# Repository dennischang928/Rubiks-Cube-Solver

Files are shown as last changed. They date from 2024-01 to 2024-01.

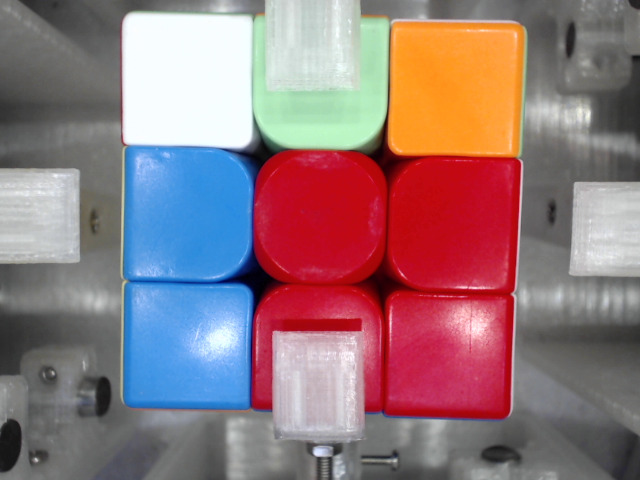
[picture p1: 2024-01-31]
Paper/DX.jpeg

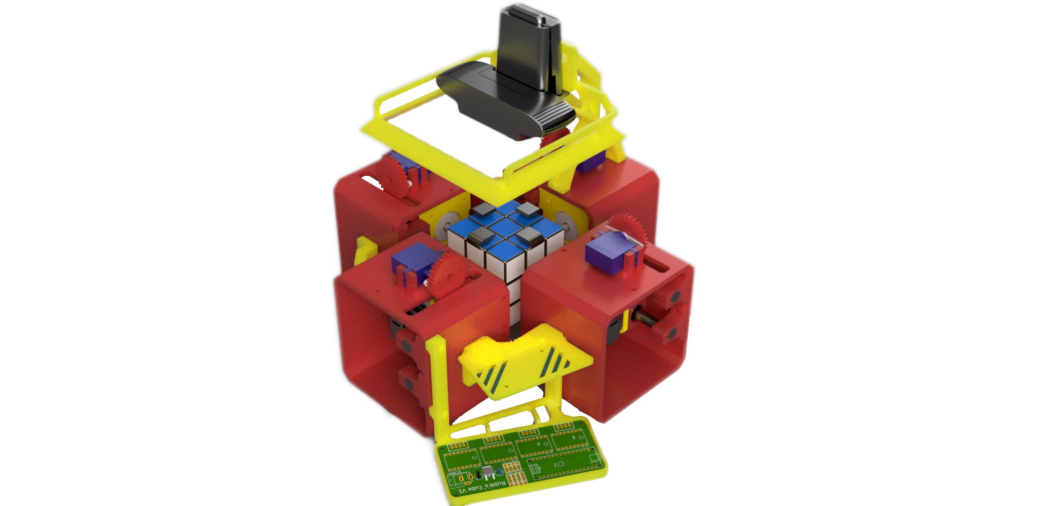
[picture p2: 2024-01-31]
Posters/Rubik_cube_solver_combine v50.png

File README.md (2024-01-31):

SubPage
# Rubik's-Cube-Solving-Robot

# Abstract

Rubik's Cube, a 3-D combination puzzle invented by Ernő Rubik in 1974, is the World’s top-selling puzzle game and best-selling toy. Rubik's Cube is surprisingly complex, there are 43,252,003,274,489,856,000 permutations of a standard 3×3×3 Rubik's Cube. Although humans are impossible to memorize all permutations of a Rubik’s Cube, humans can solve the puzzle as fast as 3.47 seconds. In recent years, a robot developed by MIT students can solve it in 0.38 seconds using an optimal algorithm.
In this project, I developed a Rubik’s Cube-solving robot using a Computer Vision algorithm from scratch. The robot has 4 stepper motors and 4 servo motors as actuators. A camera is included to observe each color arrangement of the face of the Cube in a scrambled state sequentially. The image that the camera observed will be sent through a serial interface to the computer. I implement a solving algorithm that will take the Cube state as input and the sequence of moves that solve the Cube as an output. The sequence of moves is sent to the MCU and is then translated into a series of instructions. The stepper motors and the servo motors then work together to twist the Cube according to the instructions, fully solving the Cube.

# Contents

- Abstract
- Motivation
- Introduction
- Materials
- Designs
  - Hardware
    - Actuators
    - Camera
    - Electronics
  - Programming
    - Computer vision
    - Thistlethwaite's algorithm
    - Firmware
- Challenges and Conclusion
- Reference
- Appendix — Workflow of the Rubik's Cube solving robot

# Motivation

In recent years, Computer Vision becomes more popular. Computer Vision has a lot of applications, such as object detection, event detection, video tracking, and color recognition. To familiarize myself in the field, I decide to develop a robot that solves a Rubik’s Cube using Computer Vision.
The goal is to fully solve a Rubik’s cube by twisting it using clamps attached to stepper and Servo motors. We will use a camera to capture each face of the cube. A computer will then be used, using the computer vision algorithm, to process these images and find out the color of the 9 stickers in each face. Once the color states of the cube are determined, the computer can then compute the sequence of moves that fully solve the cube.

# Introduction

I design the robot using Fusion 360 and Eagle. This robot consists of 4 stepper and Servo motors, 4 pairs of 3d-printed clamp and frame, a camera, and a PCB board with a microcontroller and 4 stepper motor drivers.



The design of the robot ^

To know the initial state of the Cube, I use a camera to capture the color of the Cube. Since the camera can only capture a single face of the Cube each time, the robot needs to rotate the Cube for the camera to capture all the faces of the cube. After capturing, the camera is going to send those images to the computer through a USB port.

The computer will then detect the position and orientation of each face from all 6 images. By using these information, the computer can find out the position and area of each sticker of the Cube in those images. The computer can now extract the color of each sticker, and determine the color of each sticker using computer vision.

Once the initial state of the Cube is found, the computer solves the Cube using Thistlethwaite's algorithm. The solution, the sequence of moves represented in Rubik's Cube Notation, will then be sent from the computer to the microcontroller. Afterwards, the microcontroller translates these notations into a series of stepper and Servo motors movements that twist the Cube and fully solve the Cube.

# Materials

- 4 stepper and Servo motors
- 4 3d-printed clamps attached to the stepper motors
- An Arduino nano and 4 stepper motor drivers
- A DC transformer
- A fill light

# Designs

## Hardware

### Actuators

To physically twist and rotate the cube, I use 4 NEMA 17 stepper motors that use a clamp to clip and twist 4 individual faces of the cube. I have considered using DC motors and brushless motors, but both of them can't know their physical rotated-angle without an encoder, so they can't twist the cube precisely.

I have considered using DC motors and brushless motors, but both of them can't twist the Cube precisely because their physical rotated-angle cannot be determined without an encoder.

Although Servo motors can rotate precisely to an angle, most Servo motors can only rotate from 0 degrees to 180 degrees. <add a reason why 0-180 is bad> Therefore, I decided to use stepper motors because they are continuous(they can rotate in one direction infinitely) and can rotate precisely. Therefore, a stepper motor will perfectly fit our use case.

Stepper motors operate using a coil to attract the permanent magnets that encircle the center axle. By energizing the coils, the axle of the motor can rotate precisely by 1.8 degrees. (Stepper motors take 200 steps to make a complete rotation, so its resolution is 1.8 degree = (360° /200 steps))

Stepper motors move in steps. For example, a stepper motor with 200 steps resolution will rotate 1.8 degrees angle for one step (360° / 200 steps).



Simplified stepper motor rotates 3 steps.

Stepper motor is an Open Loop Control System, we don't know its position upon start-up.

In order to twist the Cube properly, the clamp needs to be aligned vertically with the Cube. Therefore, I design a device that uses a distance sensor to provide feedback for the motor to align the clamp and the cube. The device consists of a disk attached to the axle of the motor and an IR Sensor facing the disk. The cube and clamp are in perfect alignment when the IR Sensor faces the hole directly. Hence, by reading the sensor value, the motor can rotate the clamp until it aligns perfectly with the cube.

螢幕截圖 2021-08-16 17.51.25.png

螢幕截圖 2021-08-16 17.51.08.png

IMG_2260.HEIC



Fig 1

I found a problem when the clamp is twisting the cube. If one of the clamps rotates horizontally, the clamps on its left and right can't twist the cube because the clamp that is horizontal blocks their rotation. Tj is also a Servo motor that is responsible to separate the clamp from the cube so that all clamps can rotate freely. As shown in the image on the left

In contrast to the stepper motor, Servo motor is a Closed Loop control system. When the Servo motor is moving, the position given by the potentiometer as feedback (Fig 1)
is sent to the Servo motor control board to ensure it rotates to the expected position.

I use Rack and pinion mechanics to convert the rotational motion of the Servo motor into linear motion to separate the clamp from the cube.

螢幕截圖 2021-08-17 11.19.00.png

### Camera

To determine the initial state of a Rubik's cube, I use a camera to capture the color of each face of the Rubik's cube. I chose a Logitech Webcam as the camera because it has HD resolution and an autofocus function. Moreover, the camera allows you to adjust the brightness, sharpness, contrast, and saturation of the image. By adjusting these values, the images will become sharper and easier for the computer to distinguish colors.

Trying to distinguish color from the image that the camera sends to the computer, I find that if the ambient light around the cube is unstable, the color recognition program will be extremely inaccurate. To make sure the projected light on the cube is consistent, I added an artificial light source to maintain the brightness of the image. Therefore, I use 4 LED strings to supply light in 4 directions, so the brightness anywhere on the face of the cube is the same.

### Electronics

Instead of using a commercial CNC control board that can control stepper motors easily, I am going to design my robot controller PCB that can control 4 stepper motors and 4 Servo motors of my robot because most commercial CNC control boards can't control 2 or more Servo motors. Also, there is a lot of limitations of programming these commercial PCB board, so I decided to make my own control board.



Robot control board

- Microcontroller

In order to control the whole robot, I decided to use Arduino nano to control the whole system because it is smaller than Arduino UNO and easy to program. Arduino Nano has a built-in Mini USB jack, so it can communicate with the computer through a Serial port with the Mini USB jack.

- Stepper Motor Control

Although stepper motors have a lot of advantages, controlling stepper motors often require sufficient and controlled energy for phases in a precise sequence, so a driver is often needed. Due to this, I plan to use 4 A4988 stepper motor drivers to control all of my stepper motors of the robot.

Each A4988 motor driver required 2 control signal pins (step, direction) and 3 setup signal pins(MS1, MS2, MS3). The step and direction pins are used to control the movement of the stepper motors. The direction pin controls the rotating direction of the motor, and we can control the movement of a step of the motor by sending a pulse to the step pin. The MS1, MS2, MS3 pins are used to control the step of the stepper motor. By changing the input state of these pins to logic low or logic high, you can select one of the five steps resolutions according to the table(Fig 2).



Fig 2

- Servo motors Control

A Servo motor can be controlled by sending a series of pulses through the signal pin. By changing the width of these pulses, we can control the Servo motor rotates to different angles.



How pulses with different widths control the Servo motor

## Programming

### Computer visions

In order to determine the color arrangement of each of the images captured by the camera precisely, I implemented a method that can find out the difference between two colors.
A color model is a visualization that depicts the color spectrum as a multidimensional model. There are some commonly used color models in the world. Most modern color models have 3 dimensions (like RGB and HSV), while other models have more dimensions (like CMYK), and I am going to compare these different color models and find out which of them are more reliable in this project.

---

- RGB

  RGB is a 3-dimensional color model. RGB color model represents a color by mixing three different colors (Red, Green, and Blue). Although RGB color model is commonly used in our daily life, RGB color model is a non-uniform color model, which means the Euclidian distance of two colors represented by the RGB color model does not correspond to the color difference perceived by humans.

  _Euclidian distance:_

  $distance=√((R2−R1)^2+(G2−G1)^2+(B2−B1)^2)$

  

---

- HSV

  HSV is a cylindrical color model that remaps the RGB primary colors into dimensions that are easier for humans to understand.

  In HSV color model, we can represent a color with 3 variables (Hue, Saturation, Value). Hue controls the angle of the color on the RGB color circle; Saturation controls the amount of color used; Value controls the brightness of the color.

  

  HSV (cylindrical color model)

---

- CIELAB

  CIELAB color model is three-dimensional, you can represent a color with 3 variables in CIELAB color model while L stands for perceptual lightness, and A and B stand for the four unique colors of human vision: red, green, blue, and yellow. In short, CIELAB is designed to approximate human vision, so it can describe a color more accurate than RGB and HSV color models can.

  

  CIELAB color space top view

According to the comparison, I think using CIELAB color model in the Computer Vision method has a lot of advantages, so I plan to use CIELAB color model to represent a color in the Computer Vision method.

When the computer wants to distinguish which color (orange, white, blue, red, yellow, green) of a sticker is, the most important thing is to find out the distance between the sticker pixel color and the reference colors, so the computer can then compare the distance between these reference colors, and distinguish the color. In order to get the color difference between two colors reliably, I use a CIEDE2000 ΔE method instead of the Euclidean distance method because the CIEDE2000 ΔE method is more reliable for human vision.

Given a reference color (L*1, a*1, b*1) and another color (L*2, a*2, b*2), the CIEDE2000 difference of these 2 colors is:



CIEDE2000 ΔE formula
[https://en.wikipedia.org/wiki/Color_difference](https://en.wikipedia.org/wiki/Color_difference)

Where:

[https://wikimedia.org/api/rest_v1/media/math/render/svg/2940920f995d52312ede05214ffa3c60f0db9b7f](https://wikimedia.org/api/rest_v1/media/math/render/svg/2940920f995d52312ede05214ffa3c60f0db9b7f)

CIEDE2000 ΔE formula
[https://en.wikipedia.org/wiki/Color_difference](https://en.wikipedia.org/wiki/Color_difference)

Because of the rotation of the cube, the cube position may always shift when scanning the cube, so I have to frequently adjust the cube detect area of the camera manually before scanning it, and I think that adjusting the cube manually is annoying, especially when I'm debugging the program.

Then, I try to implement a cube position tracking program in the solver, so that the solver can adjust the detect area automatically.

The tracking program is actually dum. First of all, the program is going to make the dimmer place of the image more dimmer; the brighter place brighter. The program can then find out the position of the centerpiece of the cube by comparing the pixel of the filtered image. The program can then find out the position of other pieces.



Image before filter



Filtered image

### Thistlethwaite's algorithm

After finding the state of the cube, the computer will then solve the cube using Thistlethwaite's algorithm. Thistlethwaite's algorithm is a famous algorithm devised by Morwen B. Thistlethwaite.

Before I explain how the algorithm works, we first have to know how do people represent a twist of a cube. People usually use a notation called Rubik's Cube Notation to represent a twist of a cube. The twist of a Rubik's Cube is classified into three categories of Notations (clockwise twist, counterclockwise twist, double clockwise twist).

- The notation with only one letter refers to a clockwise face twist in 90 degrees (quarter turn). "F" refers to a clockwise turn of the Front face in 90 degrees.
- The notation with one letter followed by an apostrophe (') refers to a counterclockwise face twist in 90 degrees (quarter turn). "D'" refers to a counterclockwise turn of the Down face in 90 degrees.
- The notation with one letter followed by the number 2 refers to a clockwise face twist in 180 degrees (double turn). "U2" refers to a clockwise turn of the Up face in 180 degrees.



Thistlethwaite algorithm solves a cube by twisting the cube by a certain set of moves. When the cube reaches a specific state, the cube will "move" from one "group" to another. As the cube reaches another "group", the set of moves of the cube will change and the cube will be easier to solve computationally.

The groups are:

- Group 0:

[https://wikimedia.org/api/rest_v1/media/math/render/svg/2dbdffdebca6e844bdf3c7548a8033992ef6ac79](https://wikimedia.org/api/rest_v1/media/math/render/svg/2dbdffdebca6e844bdf3c7548a8033992ef6ac79)

Required Cube state: This group contains all possible states of the Rubik's Cube.

---

- Group 1:

[https://wikimedia.org/api/rest_v1/media/math/render/svg/116b5e3559d97ddaa688362537461712c1435f10](https://wikimedia.org/api/rest_v1/media/math/render/svg/116b5e3559d97ddaa688362537461712c1435f10)

Required Cube state: All 12 edge pieces are correctly oriented.

After reaching Group 1, The cube can then be solved without using U and D turns.

---

- Group 2:

[https://wikimedia.org/api/rest_v1/media/math/render/svg/ab29e5a1ef0d23014458f9603f6c108b7aec73a6](https://wikimedia.org/api/rest_v1/media/math/render/svg/ab29e5a1ef0d23014458f9603f6c108b7aec73a6)

Required Cube state: All corner pieces are correctly oriented. Also, four of the edge pieces are moved to the correct slice: the front-up, front-down, back-up, and back-down edge pieces are placed in the M slice.

After reaching Group 2, The cube can then be solved without using F, B, U, and D moves.

---

- Group 3:

[https://wikimedia.org/api/rest_v1/media/math/render/svg/b9990ca7e1121afb33509d738d77f1d0c455be62](https://wikimedia.org/api/rest_v1/media/math/render/svg/b9990ca7e1121afb33509d738d77f1d0c455be62)

Required Cube state: All corner pieces are moved to the correct orbit. (A corner is in the correct orbit if it can be moved to its home position with only 180-degree twists.) Also, each edge piece is moved to its home slice.

At that point, the cube can be solved with only 180 degrees turn.

---

- Group 4:

[https://wikimedia.org/api/rest_v1/media/math/render/svg/27929bbe730561ca9eb1540e72756b5674436bb5](https://wikimedia.org/api/rest_v1/media/math/render/svg/27929bbe730561ca9eb1540e72756b5674436bb5)

The final group requires only one state, which is a solved cube.

### Firmware

In this project, I use Arduino nano board as my microcontroller to control the stepper motors and servo motors. I implement an Arduino stepper motor driver library in the Arduino board to control the movement of the Stepper motors. For the Servo motors, I use an Arduino built-in Servo library to control them.



There is a lot of ways to communicate between the computer and the Arduino board, such as I2C, Serial communication, and SPI. I decided to use the Serial communication way because it is widely used in the Arduino board (Every Arduino board has its own Serial port). For an Arduino Nano board, it has a built-in mini-USB jack

Here is a case of communication:

The Computer aims to twist the Cube in U U2 D2:

**Step 1:** The computer sends a command("U U2 D2") to the Solver through the Serial interface.

**Step 2:** The Solver receives the command and controls the Stepper motors and the Servo motors to twist the Cube according to the command.

**Step 3:** After twisting the cube, the Solver will send a signal to the computer. Let the computer knows that it has done the task.



# Challenges and Conclusion

After assembling the Solver, there are some problems that I have experienced. When designing this robot, I aim to use a magnetic encoder to monitor the position of the Stepper motor. After I fully assembled the Solver, I try to read the value of the magnetic encoders by connecting them in parallel using I2C, but then I found that these magnetic encoders have the same I2C addresses, and I can't change the addresses. Therefore, the microcontroller can't read the values of them using I2C, so I have redesigned the robot, and I use a light sensor as the position monitoring sensor instead of a magnetic sensor.

There are also some challenges that I have gone through when I programming the robot, such as the inaccuracy of the color detection. To fix the issue, I add an artificial light source to stabilize the light condition of the cube.

The robot also experienced some issues when the stepper motor rotate. Because the stepper motor provides no feedback to the microcontroller, the stepper motor can't affirm a perfect 90 degrees twist is executed. Also, there are gaps between the clamp and the Cube, so there will be some degrees of error when twisting the cube. As a result, slight errors accumulated in the alignment of the Cube after a twist. Because of the alignment of the Cube, the rotation of the stepper motor may be stuck, but the stepper motor can't realize that it is stuck, and it will keep executing the following twists.

Were I to continue work on this project, the following attributes would be changed:

- A Feedback would be added to affirm a perfect 90 degrees twist is executed
- Reduce the size of the Robot.
- Design an adjustable clamp, so that the solver can fit any size of 3\*3 Rubik's Cube.

# Appendix — Workflow of the Rubik's Cube solving robot:

WorkFlow diagram of a Solver.svg

Rubik's Cube Solving Robot test:
[https://youtu.be/ZOZHCysa5HY](https://youtu.be/ZOZHCysa5HY)

# Reference

- Color models and color spaces [https://programmingdesignsystems.com/color/color-models-and-color-spaces/](https://programmingdesignsystems.com/color/color-models-and-color-spaces/)
- Color difference - Wikipedia [https://en.wikipedia.org/wiki/Color_difference](https://en.wikipedia.org/wiki/Color_difference)
- How to control stepper motor with A4988 driver and Arduino [https://howtomechatronics.com/tutorials/arduino/how-to-control-stepper-motor-with-a4988-driver-and-arduino/](https://howtomechatronics.com/tutorials/arduino/how-to-control-stepper-motor-with-a4988-driver-and-arduino/)
- jeswiezy_Project_Final_Report
  [http://web.mit.edu/6.111/www/f2017/projects/jeswiezy_Project_Final_Report.pdf](http://web.mit.edu/6.111/www/f2017/projects/jeswiezy_Project_Final_Report.pdf)
- Thistlethwaite's 52-move algorithm
  [https://www.jaapsch.net/puzzles/thistle.htm](https://www.jaapsch.net/puzzles/thistle.htm)
- Rubik’s Cube Reconstruction from Single View for Service Robots
  [https://www.ia.pw.edu.pl/~wkasprza/PAP/ICCVG06.pdf](https://www.ia.pw.edu.pl/~wkasprza/PAP/ICCVG06.pdf)
- All About Stepper Motors
  [https://learn.adafruit.com/all-about-stepper-motors/what-is-a-stepper-motor](https://learn.adafruit.com/all-about-stepper-motors/what-is-a-stepper-motor)

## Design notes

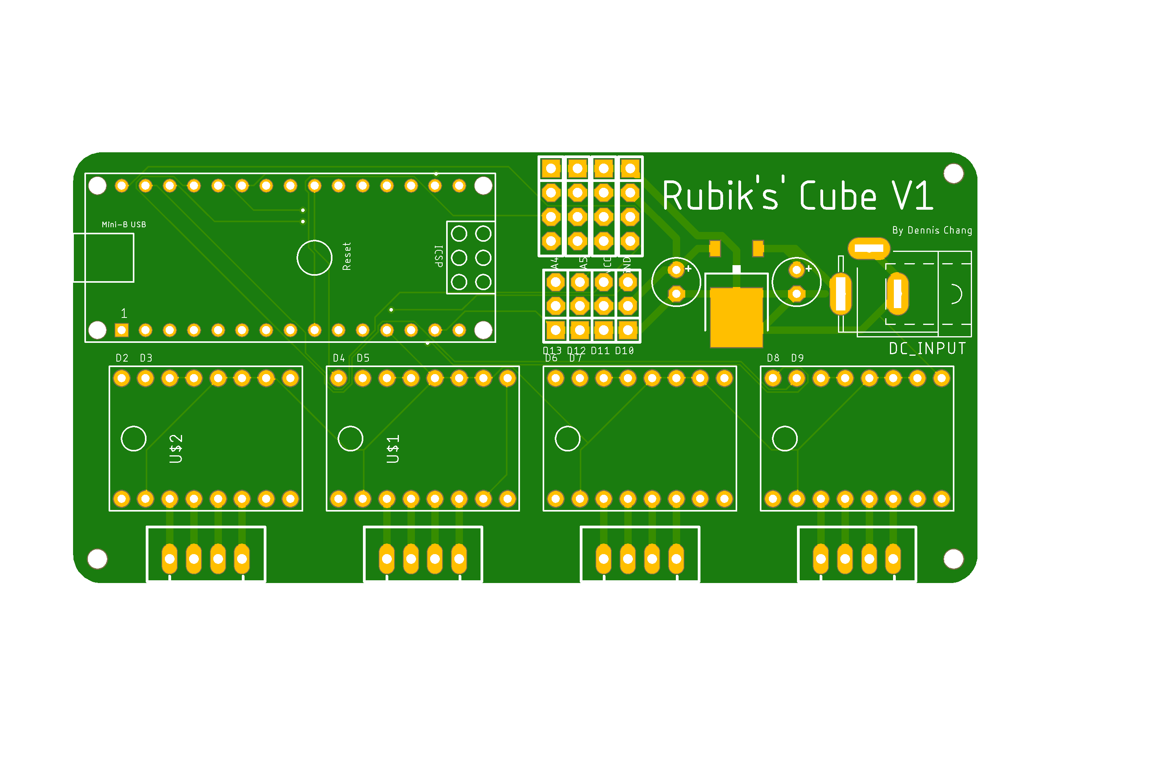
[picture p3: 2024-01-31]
Design/Circuit/V1.png

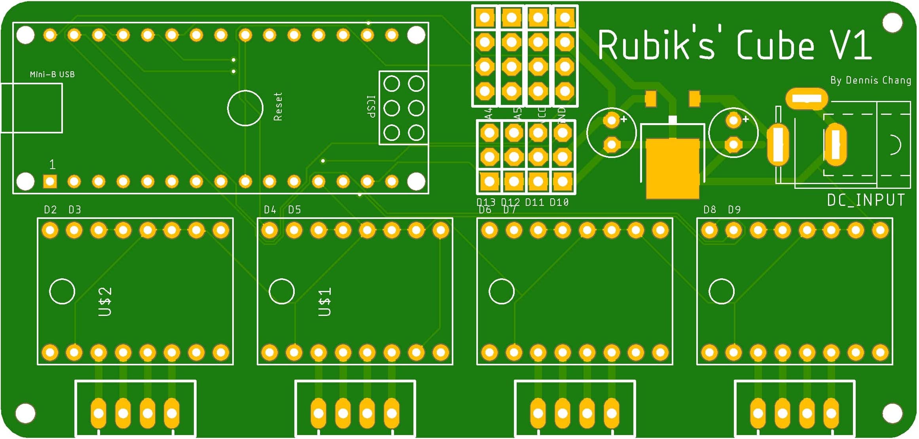
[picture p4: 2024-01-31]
Posters/PCB.jpeg

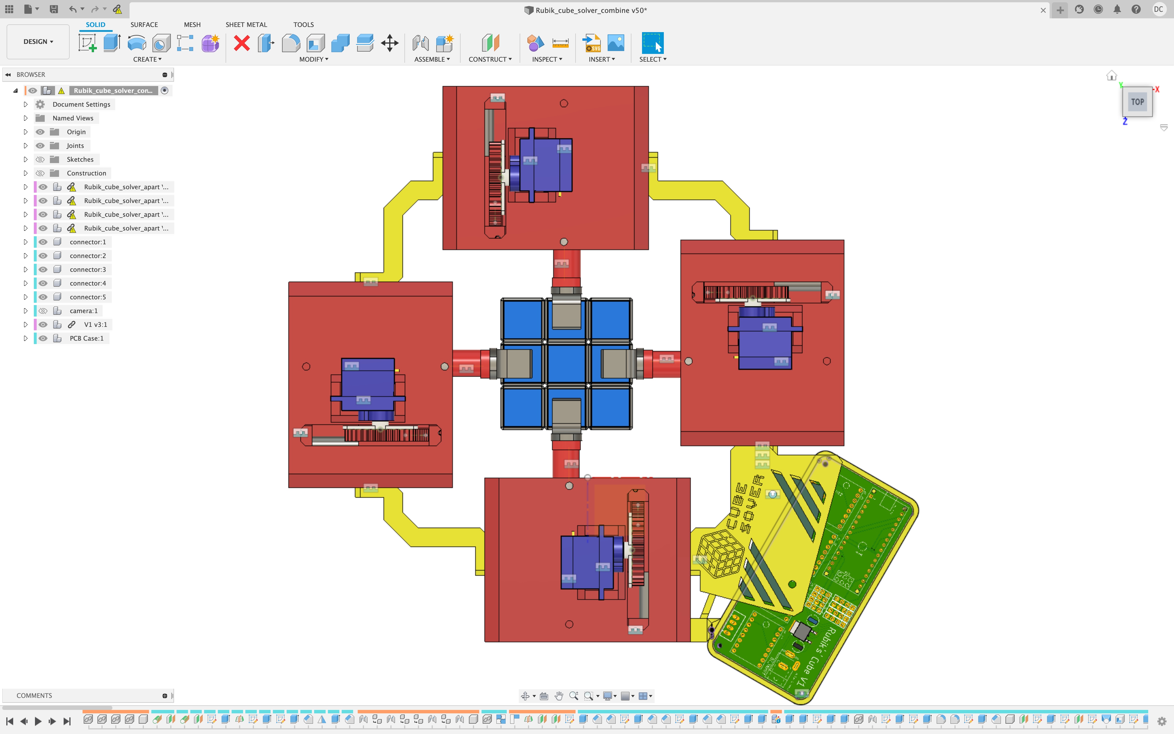
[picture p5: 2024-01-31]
Posters/螢幕截圖 2021-09-24 22.40.52.png

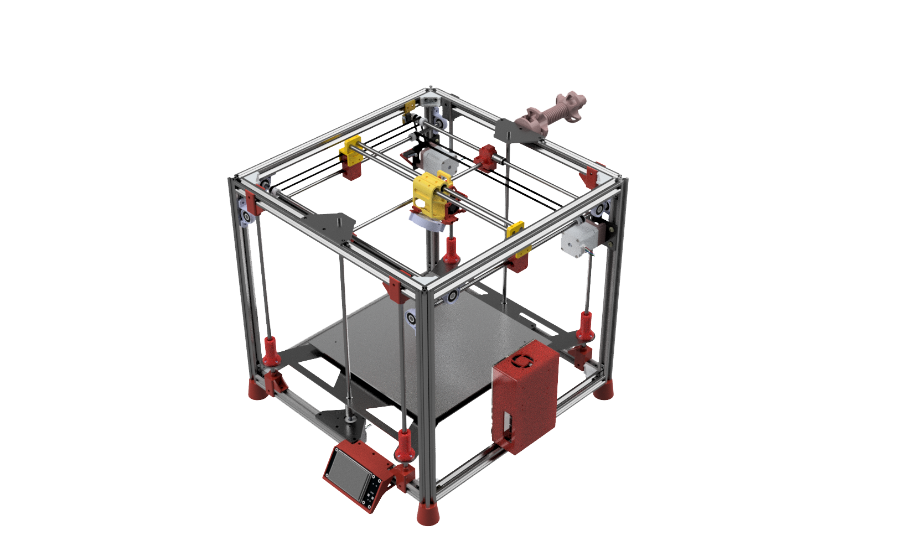
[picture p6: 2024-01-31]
Posters/3dp 5 MK2 v33.png

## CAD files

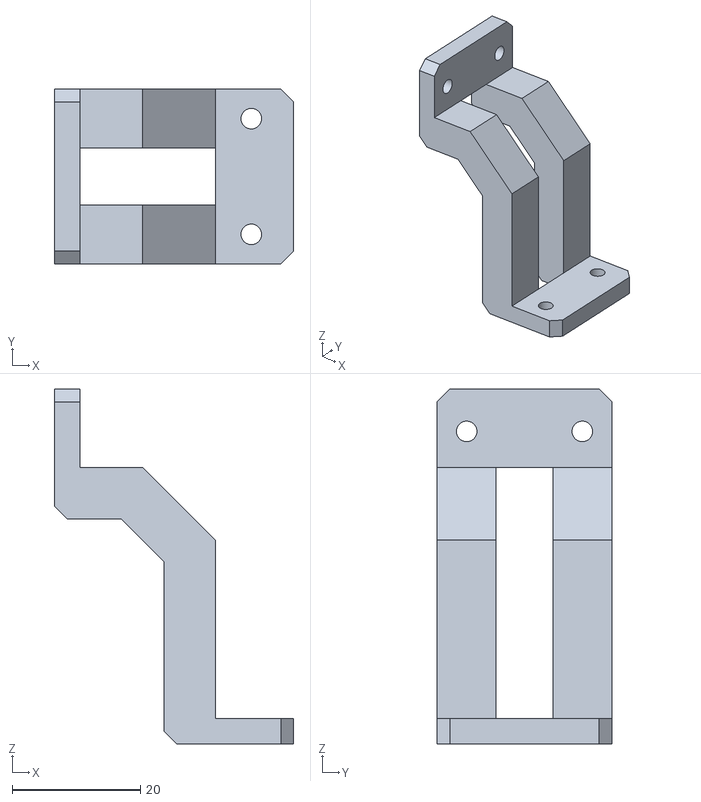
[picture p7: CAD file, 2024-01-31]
stl/com_connect.stl
37.3 x 27.2 x 55.3

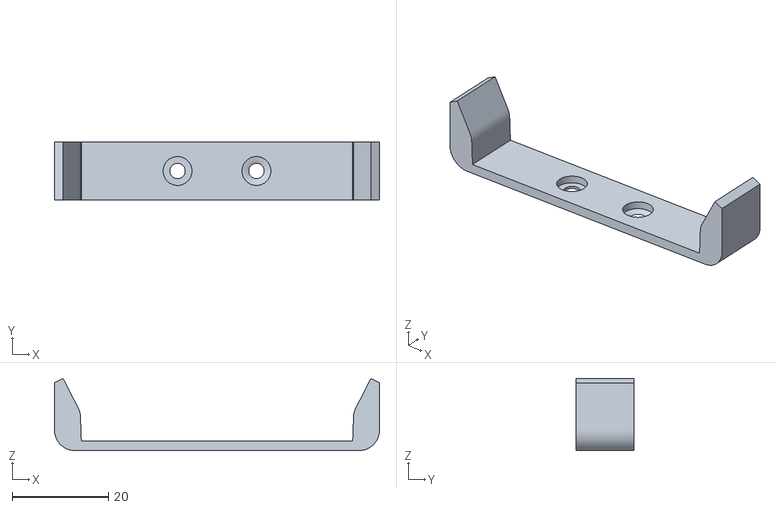
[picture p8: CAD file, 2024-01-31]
stl/v2stl/clips1.stl
67.6 x 12.1 x 15.0

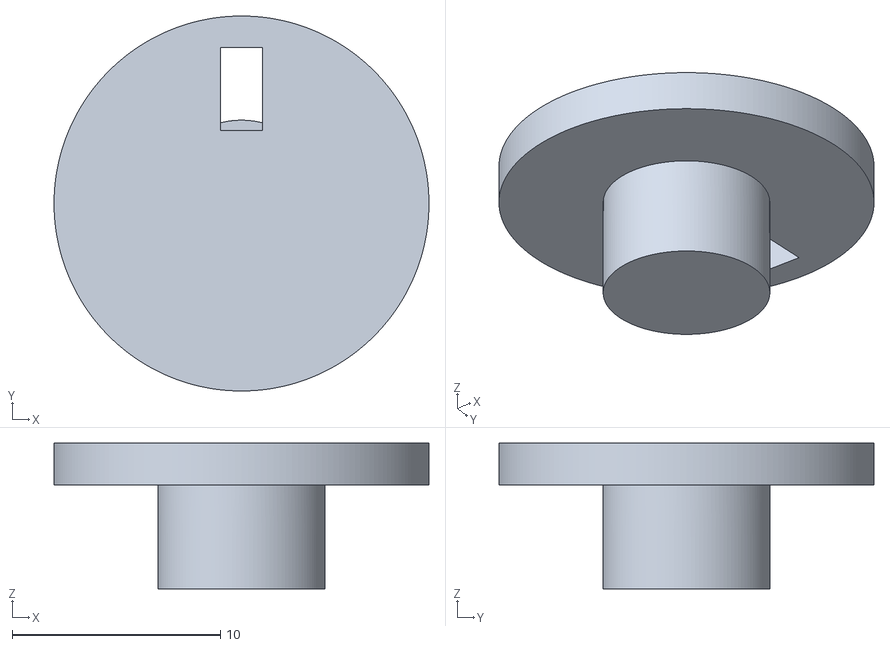
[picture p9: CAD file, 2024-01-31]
stl/rotation plate.stl
18.0 x 18.0 x 7.00

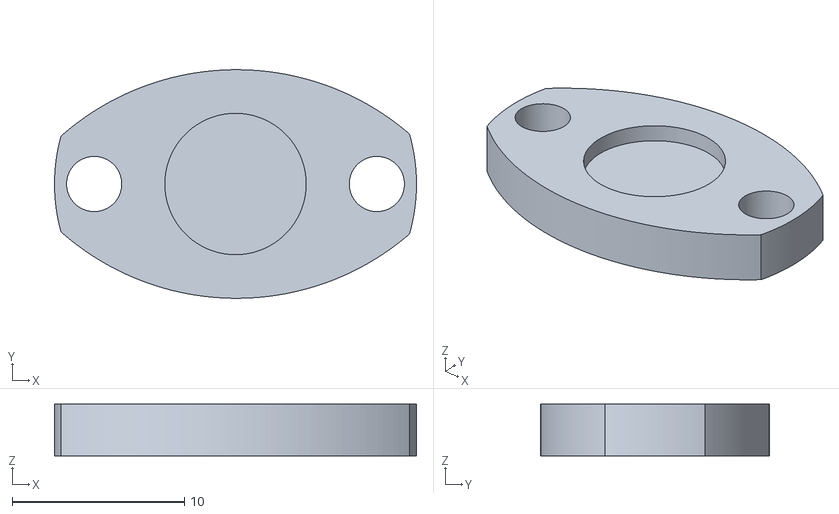
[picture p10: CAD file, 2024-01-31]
stl/v2stl/clips2.stl
21.0 x 13.3 x 3.00

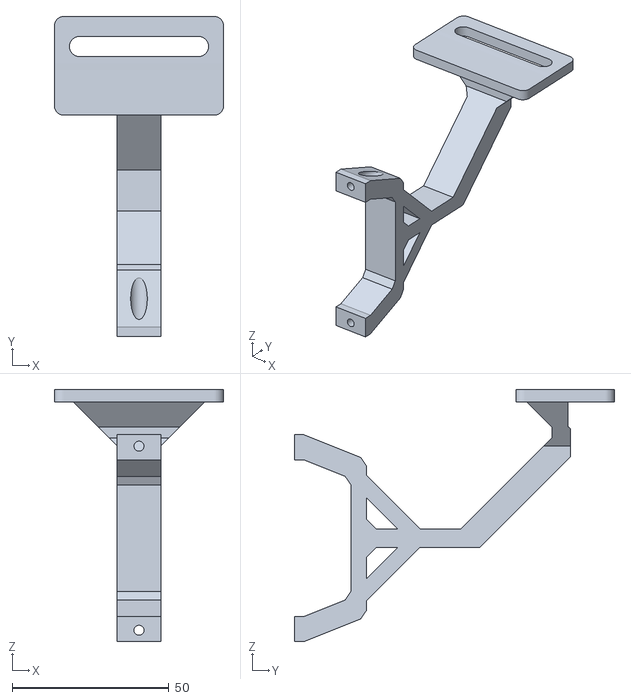
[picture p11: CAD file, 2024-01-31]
stl/camera connector.stl
54.0 x 102.1 x 80.5

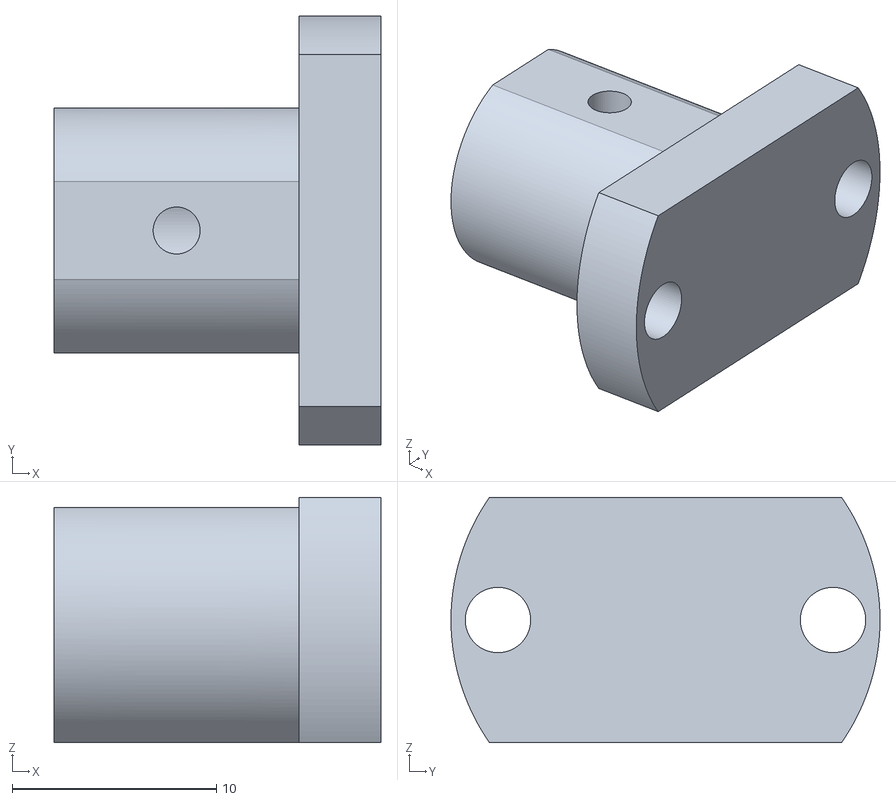
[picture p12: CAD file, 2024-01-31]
stl/v2stl/connector.stl
16.0 x 21.0 x 12.0

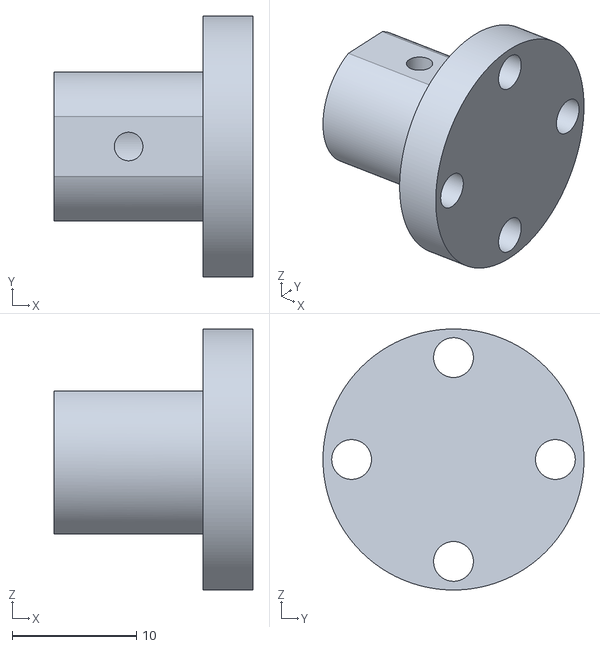
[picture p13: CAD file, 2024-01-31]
stl/stepper_connector.stl
16.0 x 21.0 x 21.0

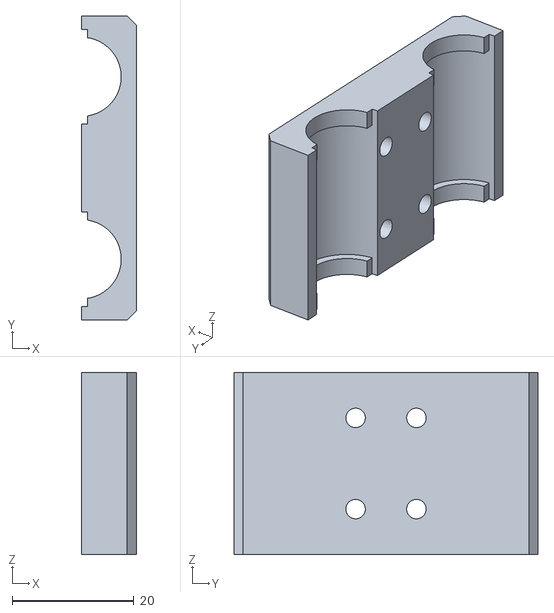
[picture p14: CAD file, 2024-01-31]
stl/move2.stl
9.00 x 50.0 x 30.0

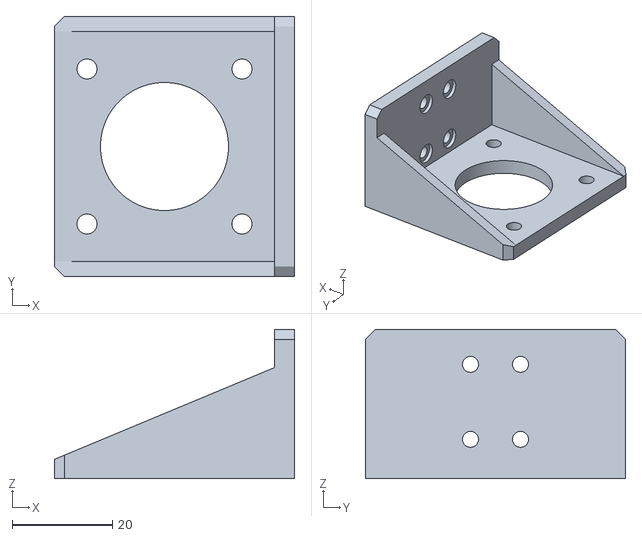
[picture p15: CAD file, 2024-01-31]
stl/stepper.stl
48.0 x 52.0 x 29.9

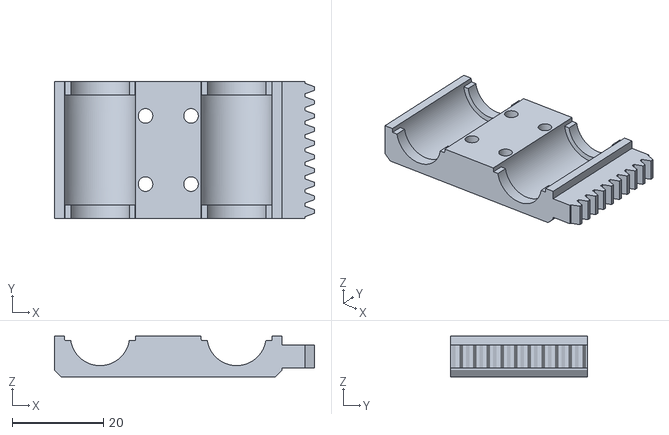
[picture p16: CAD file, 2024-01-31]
stl/move1.stl
57.1 x 30.0 x 9.00

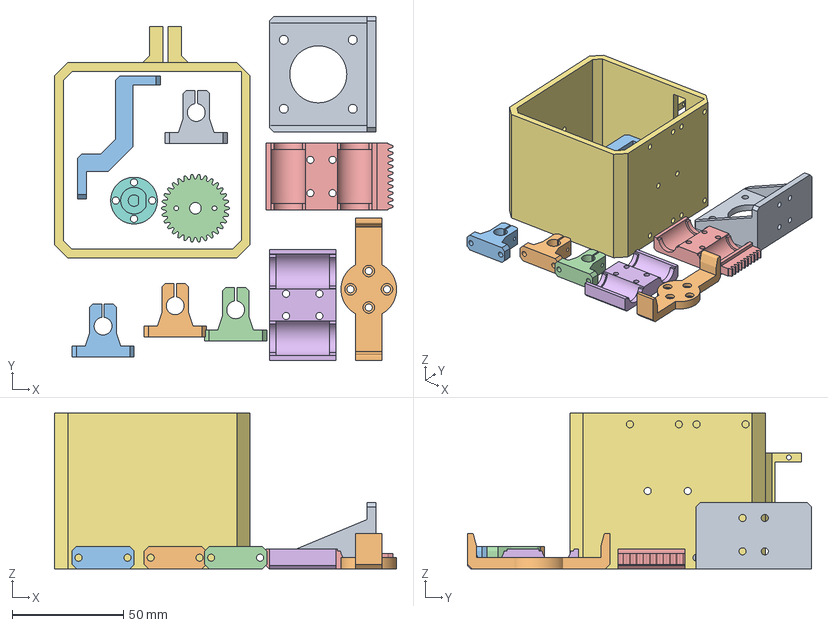
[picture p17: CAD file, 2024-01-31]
stl/rubik's cube v2.3mf
153.8 x 154.7 x 70.0 mm
axis con.stl x 4
clip.stl
com_connect.stl
gear.stl
move1.stl
move2.stl
shell.stl
stepper_connector.stl
stepper.stl

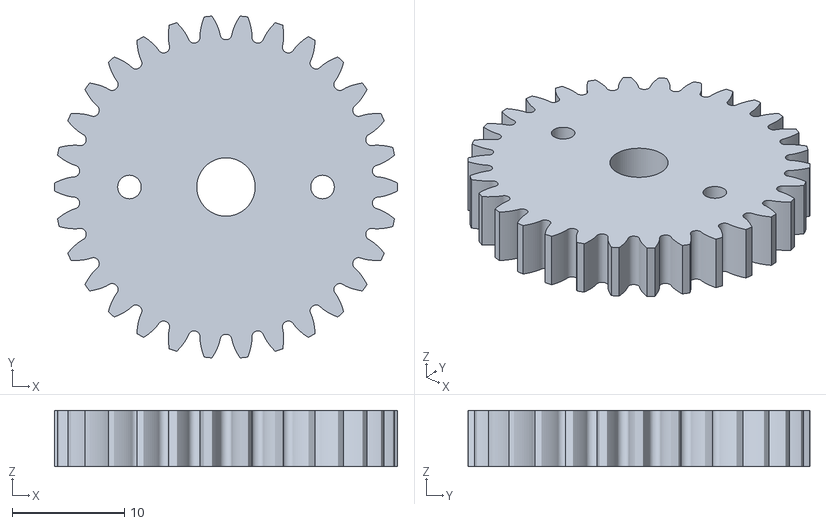
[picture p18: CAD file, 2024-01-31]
stl/gear.stl
30.6 x 30.5 x 5.00

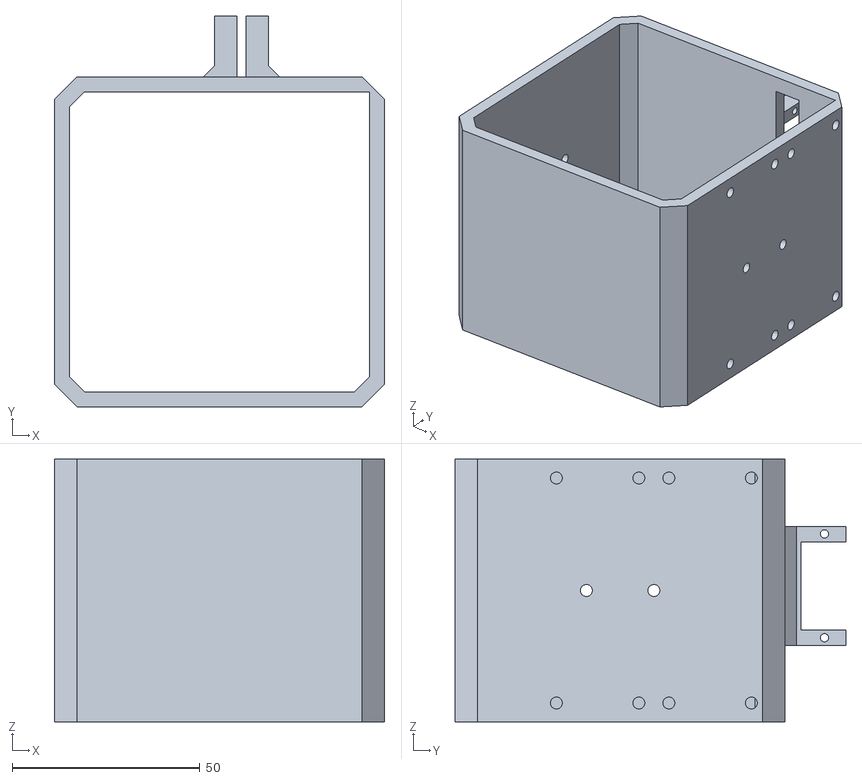
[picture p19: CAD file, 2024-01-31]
stl/shell.stl
88.0 x 104.2 x 70.0

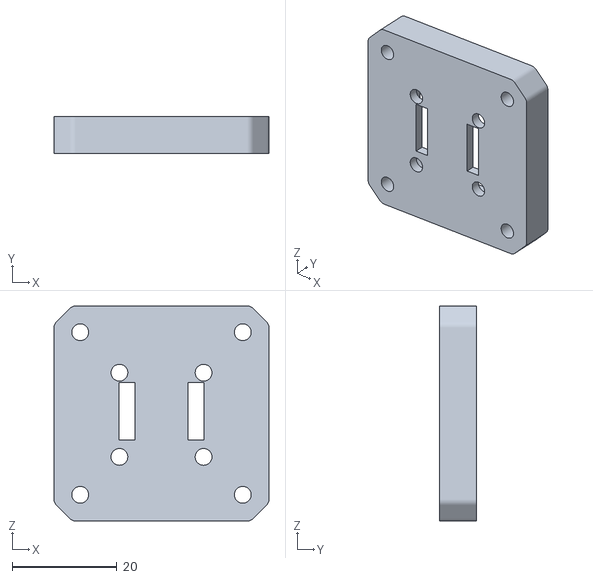
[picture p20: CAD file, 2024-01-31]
stl/encoder_Cover.stl
41.0 x 7.00 x 41.0

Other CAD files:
Pic/Untitled.dwg
stl/encoder.stl
stl/axis con.stl
stl/clip.stl

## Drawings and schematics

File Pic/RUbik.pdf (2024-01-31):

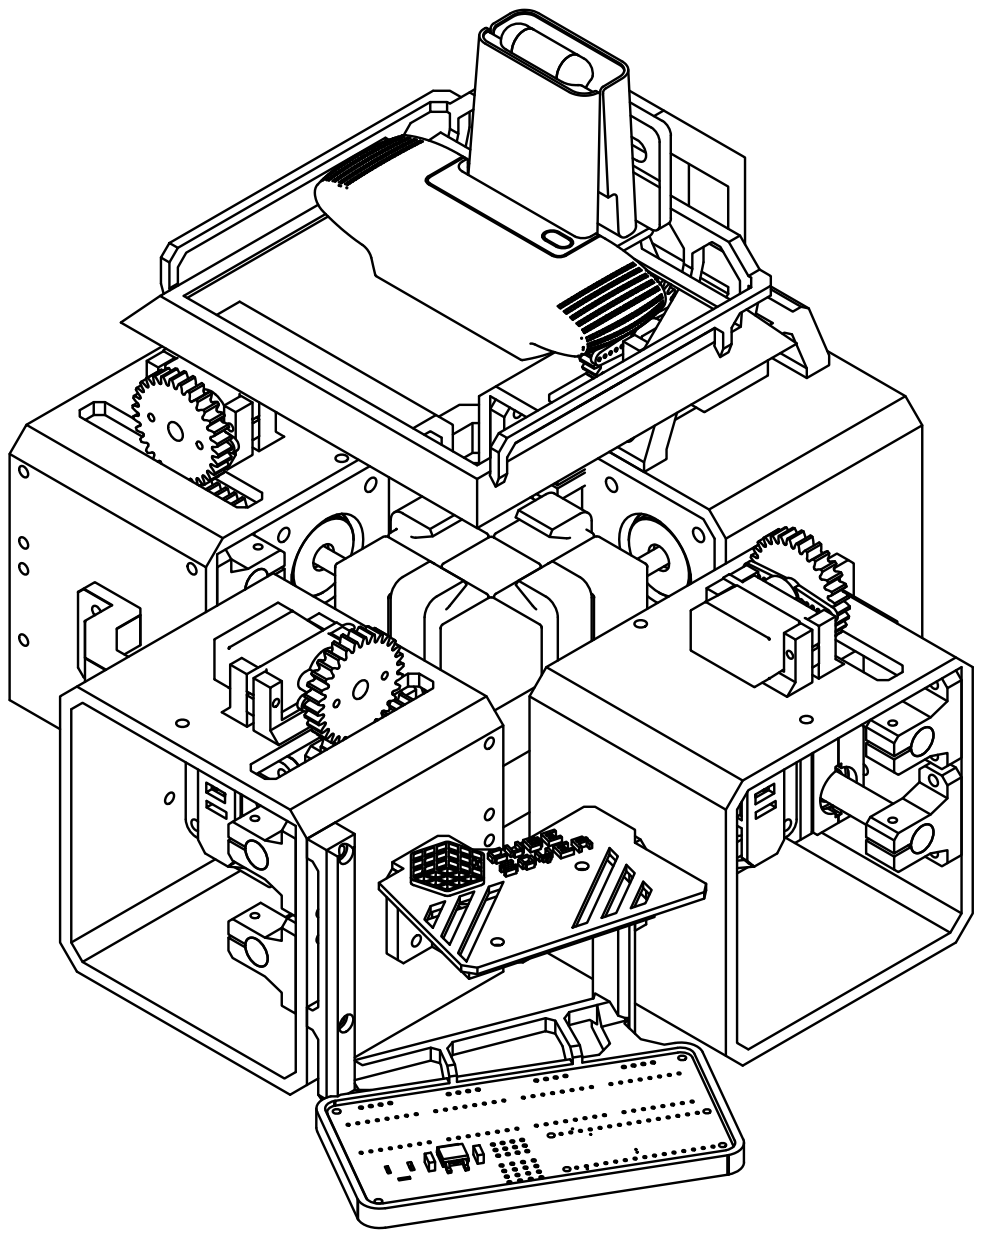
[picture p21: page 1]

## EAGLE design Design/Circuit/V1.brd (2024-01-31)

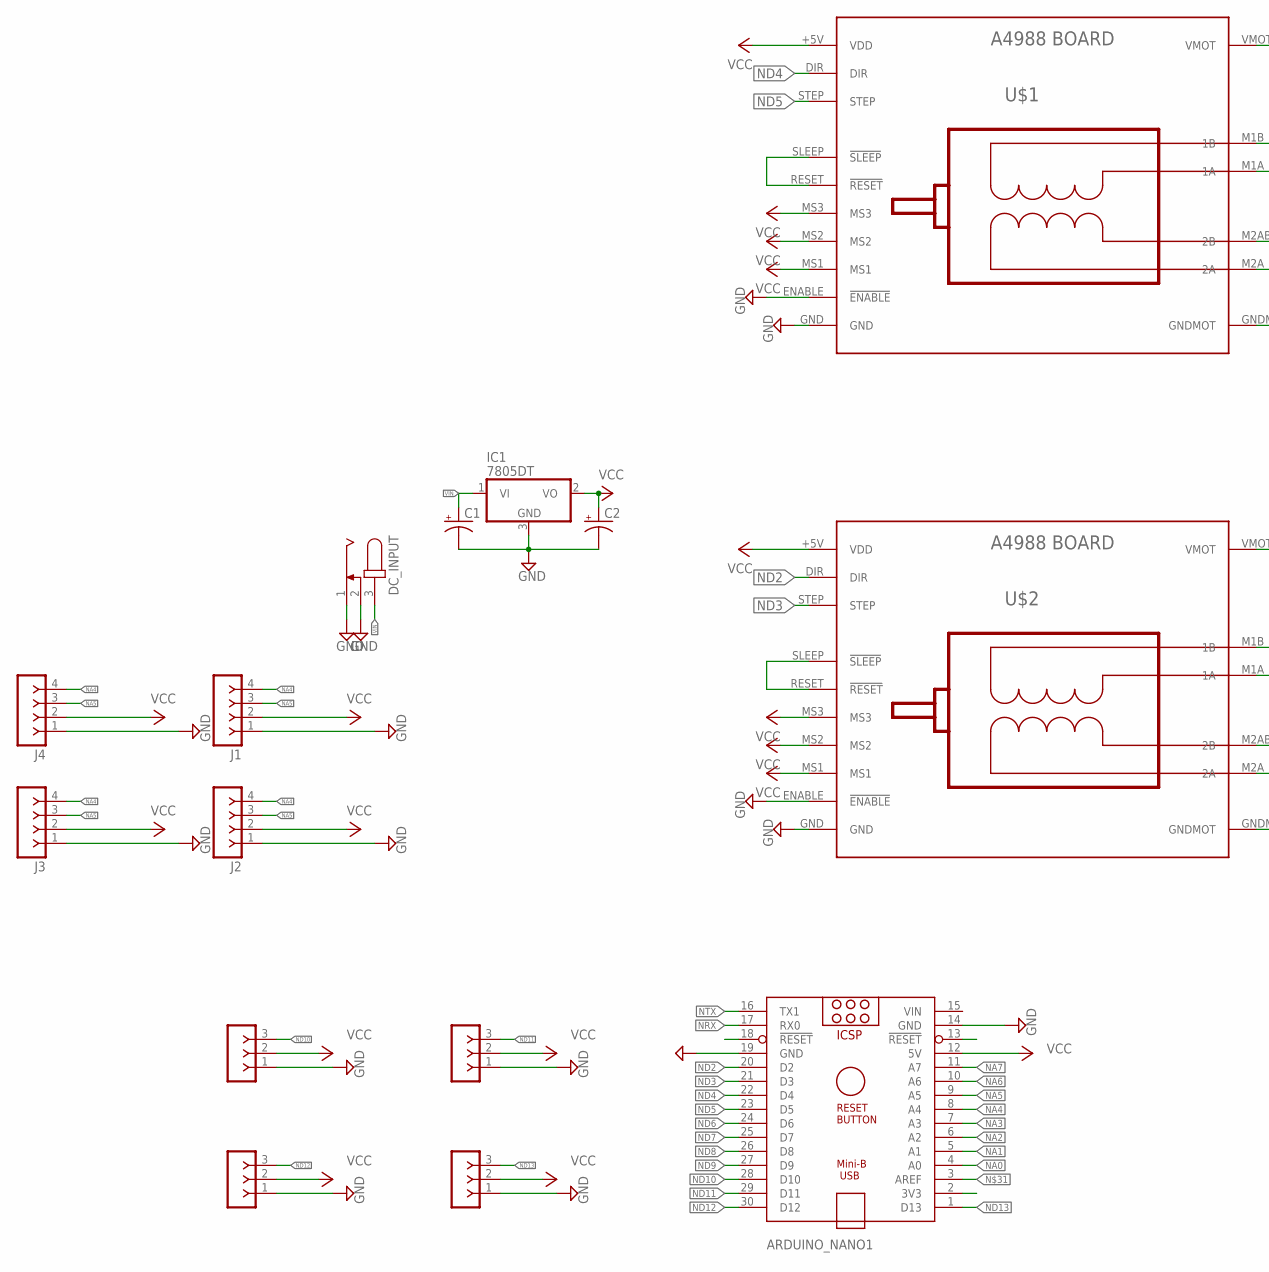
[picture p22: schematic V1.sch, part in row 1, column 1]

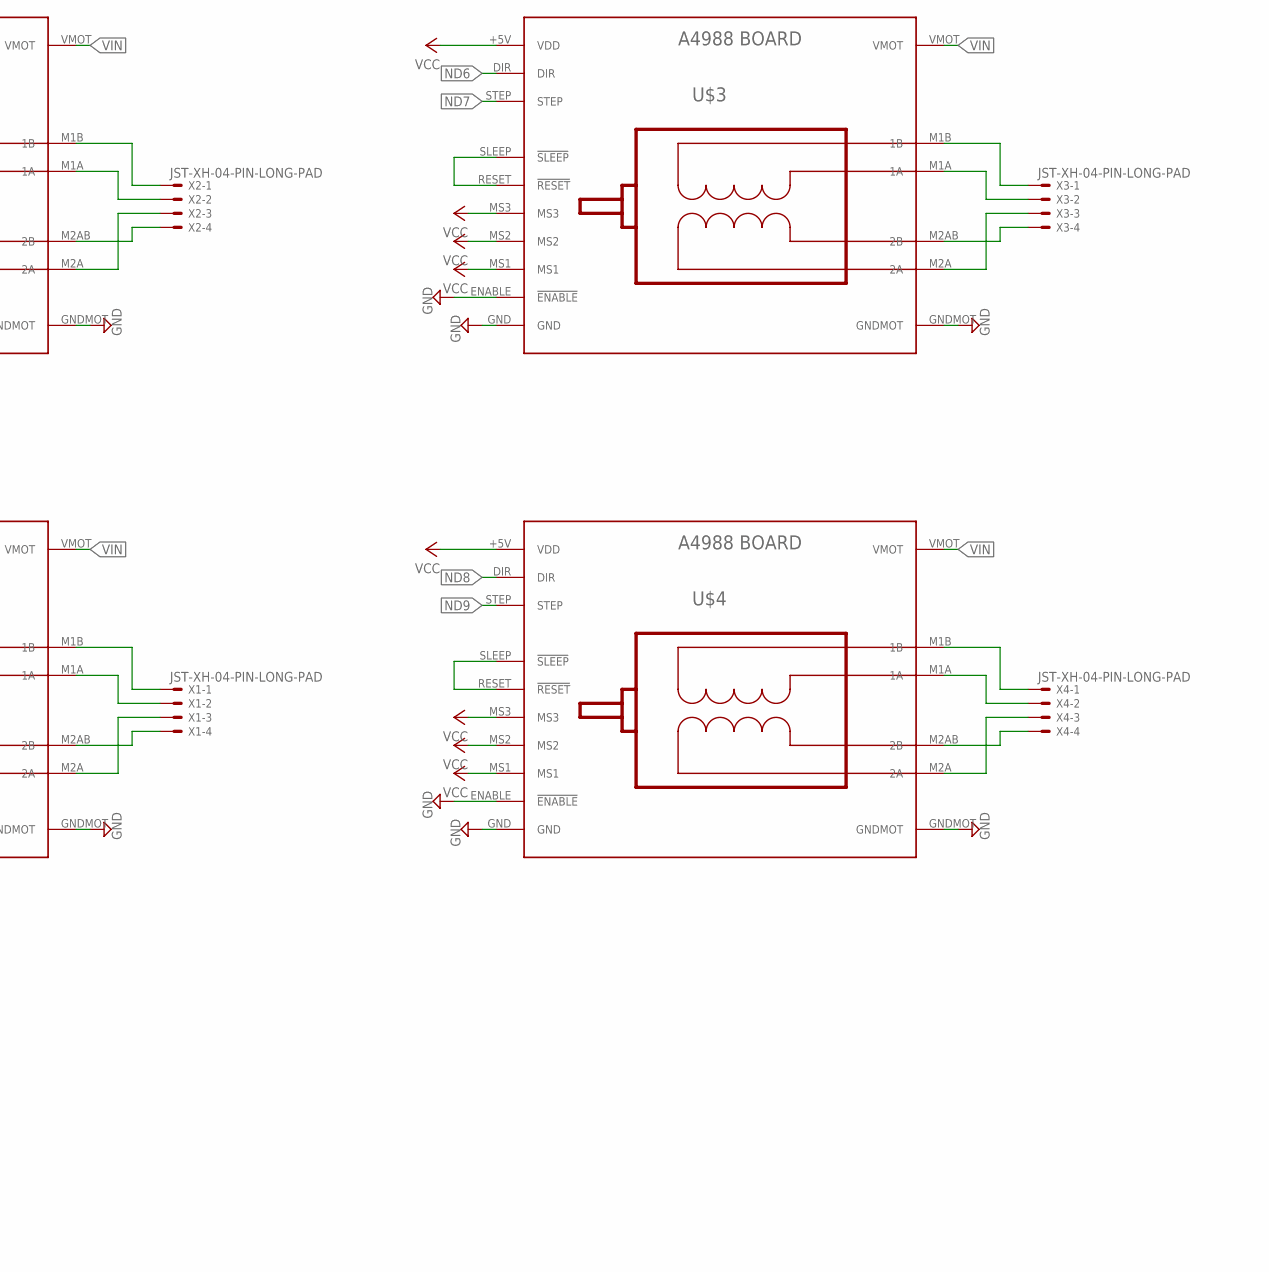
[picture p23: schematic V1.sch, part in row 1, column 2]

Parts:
ARDUINO_NANO1: ARDUINO_NANO
C1, C2: CPOL-USE2.5-5; E2,5-5
DC_INPUT: JACK-PLUG0; SPC4077
IC1: 7805DT; TO252
J1, J2, J3, J4: F-1X04-SIP-100-40; SIP-100-04-40
SERVO1, SERVO2, SERVO3, SERVO4: F-1X03-SIP-100-40; SIP-100-03-40
U$1, U$2, U$3, U$4: BOARD_A4988
X1, X2, X3, X4: JST-XH-04-PIN-LONG-PAD; JST-XH-04-PACKAGE-LONG-PAD

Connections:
GND: ARDUINO_NANO1.14 (GND), ARDUINO_NANO1.19 (GND), C1.-, C2.-, DC_INPUT.1, DC_INPUT.2, IC1.3 (GND), J1.1, J2.1, J3.1, J4.1, SERVO1.1, SERVO2.1, SERVO3.1, SERVO4.1, U$1.ENABLE (!ENABLE), U$1.GND, U$1.GNDMOT, U$2.ENABLE (!ENABLE), U$2.GND, U$2.GNDMOT, U$3.ENABLE (!ENABLE), U$3.GND, U$3.GNDMOT, U$4.ENABLE (!ENABLE), U$4.GND, U$4.GNDMOT
unnamed: U$2.M1B (1B), X1.1
unnamed: U$2.M1A (1A), X1.2
unnamed: U$2.M2A (2A), X1.3
unnamed: U$2.M2AB (2B), X1.4
unnamed: U$1.M1B (1B), X2.1
unnamed: U$1.M1A (1A), X2.2
unnamed: U$1.M2A (2A), X2.3
unnamed: U$1.M2AB (2B), X2.4
unnamed: U$2.RESET (!RESET), U$2.SLEEP (!SLEEP)
unnamed: U$1.RESET (!RESET), U$1.SLEEP (!SLEEP)
unnamed: U$3.M1B (1B), X3.1
unnamed: U$3.M1A (1A), X3.2
unnamed: U$3.M2A (2A), X3.3
unnamed: U$3.M2AB (2B), X3.4
unnamed: U$3.RESET (!RESET), U$3.SLEEP (!SLEEP)
unnamed: U$4.M1B (1B), X4.1
unnamed: U$4.M1A (1A), X4.2
unnamed: U$4.M2A (2A), X4.3
unnamed: U$4.M2AB (2B), X4.4
unnamed: U$4.RESET (!RESET), U$4.SLEEP (!SLEEP)
NA0: ARDUINO_NANO1.4 (A0)
NA1: ARDUINO_NANO1.5 (A1)
NA2: ARDUINO_NANO1.6 (A2)
NA3: ARDUINO_NANO1.7 (A3)
NA4: ARDUINO_NANO1.8 (A4), J1.4, J2.4, J3.4, J4.4
NA5: ARDUINO_NANO1.9 (A5), J1.3, J2.3, J3.3, J4.3
NA6: ARDUINO_NANO1.10 (A6)
NA7: ARDUINO_NANO1.11 (A7)
ND2: ARDUINO_NANO1.20 (D2), U$2.DIR
ND3: ARDUINO_NANO1.21 (D3), U$2.STEP
ND4: ARDUINO_NANO1.22 (D4), U$1.DIR
ND5: ARDUINO_NANO1.23 (D5), U$1.STEP
ND6: ARDUINO_NANO1.24 (D6), U$3.DIR
ND7: ARDUINO_NANO1.25 (D7), U$3.STEP
ND8: ARDUINO_NANO1.26 (D8), U$4.DIR
ND9: ARDUINO_NANO1.27 (D9), U$4.STEP
ND10: ARDUINO_NANO1.28 (D10), SERVO1.3
ND11: ARDUINO_NANO1.29 (D11), SERVO2.3
ND12: ARDUINO_NANO1.30 (D12), SERVO3.3
ND13: ARDUINO_NANO1.1 (D13), SERVO4.3
NRX: ARDUINO_NANO1.17 (RX0)
NTX: ARDUINO_NANO1.16 (TX1)
VCC: ARDUINO_NANO1.12 (5V), C2.+, IC1.2 (VO), J1.2, J2.2, J3.2, J4.2, SERVO1.2, SERVO2.2, SERVO3.2, SERVO4.2, U$1.+5V (VDD), U$1.MS1, U$1.MS2, U$1.MS3, U$2.+5V (VDD), U$2.MS1, U$2.MS2, U$2.MS3, U$3.+5V (VDD), U$3.MS1, U$3.MS2, U$3.MS3, U$4.+5V (VDD), U$4.MS1, U$4.MS2, U$4.MS3
VIN: ARDUINO_NANO1.15 (VIN), C1.+, DC_INPUT.3, IC1.1 (VI), U$1.VMOT, U$2.VMOT, U$3.VMOT, U$4.VMOT

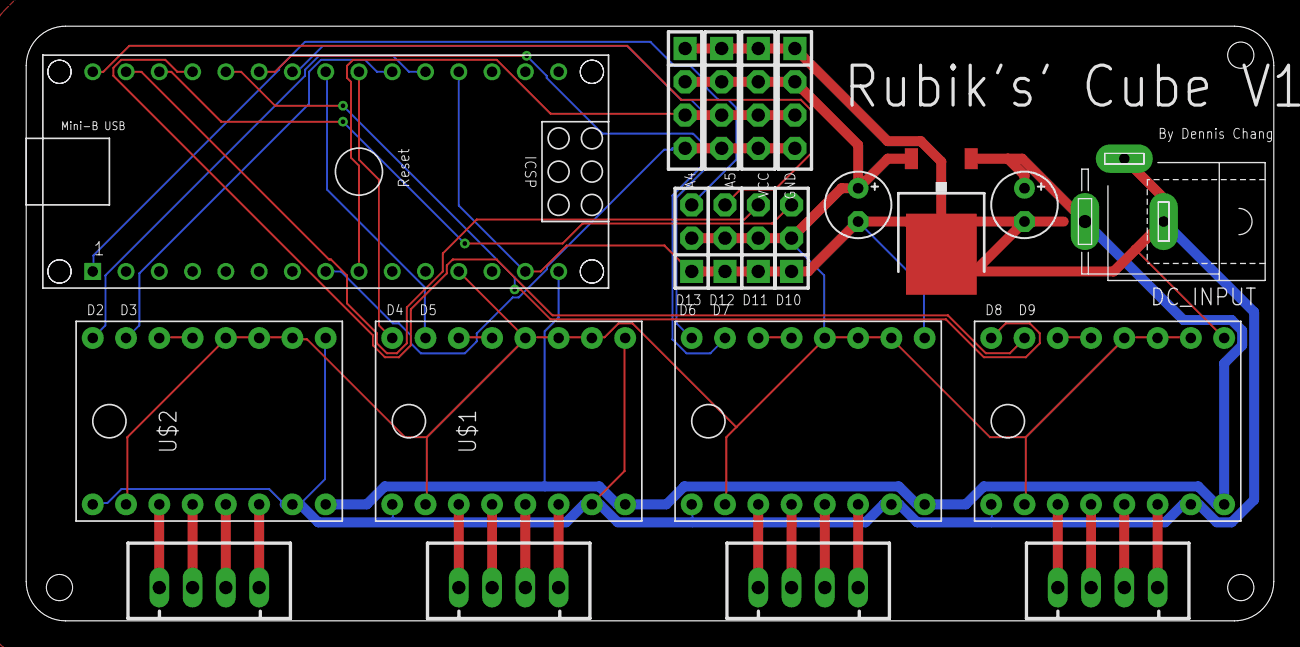
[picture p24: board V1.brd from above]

Board: 2 copper layers, 95.2 x 45.4 mm, 21 parts (0 on the bottom side), 37 nets.

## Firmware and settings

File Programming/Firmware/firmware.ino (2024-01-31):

#include <Arduino.h>
#include <Servo.h>
#include "BasicStepperDriver.h".
#include "MultiDriver.h"
#include "SyncDriver.h"
#define MICROSTEPS 16
#define MOTOR_STEPS 200
BasicStepperDriver stepper1(MOTOR_STEPS, 2, 3);
BasicStepperDriver stepper2(MOTOR_STEPS, 4, 5);
BasicStepperDriver stepper3(MOTOR_STEPS,` 6, 7);
BasicStepperDriver stepper4(MOTOR_STEPS, 8, 9);

SyncDriver stepper1_3(stepper1, stepper3);
SyncDriver stepper2_4(stepper2, stepper4);

//----------------------------------Classes----------------------------------

char input = ' ';
String Sinput = "";
int encoder_value[4];
boolean finishhome = false;
boolean DEBUG = false;
char index[6] = {'L', 'B', 'R', 'F', 'U', 'D'};
struct Send
{
  int en_cen_value[4] = {
      289,
      374,
      351,
      422,
  };
};

Send setting;
int servoPin[4] = {10, 11, 12, 13};
byte encoderPin[4] = {A5, A4, A0, A1};
int NEIGHBOR[4][2] = {{1, 3}, {2, 0}, {3, 1}, {0, 2}};

Servo servo[4];

void setup()
{
  Serial.begin(115200);
  for (int x = 0; x < 2; x++)
  {
    for (int i = 0; i < 4; i++)
    {
      pinMode(encoderPin[i], INPUT);
      servo[i].attach(servoPin[i]);
      servo[i].write(88);
    }
  }

  stepper1.begin(100, MICROSTEPS);
  stepper2.begin(100, MICROSTEPS);
  stepper3.begin(100, MICROSTEPS);
  stepper4.begin(100, MICROSTEPS);
  stepper1_3.setMicrostep(16);
  stepper2_4.setMicrostep(16);
}

class Steppers
{
public:
  int Center[4] = {0, 0, 0, 0};
  int posit[4] = {0, 0, 0, 0};
  int pos[4] = {0, 0, 0, 0};

  void Set_CTR(int index, int CTR)
  {
    Center[index] = CTR;
  }
  void reset_pos()
  {
    for (int i = 0; i < 4; i++)
    {
      if (posit[i] >= 3200)
      {
        posit[i] = 0;
      }
      if (posit[i] < 0)
      {
        posit[i] = 3199;
      }
    }
  }
  bool Move(int index, int rotate)
  {

    if (index == 0 || index == 2)
    {
      switch (rotate)
      {
      case 0:

        if (index == 0)
        {
          stepper1_3.move(1, 0);
        }
        else
        {
          stepper1_3.move(0, 1);
        }

        posit[index]++;
        pos[index]++;
        reset_pos();
        if (pos[index] >= 800)
        {
          pos[index] = 0;
          return (true);
          Serial.println("dsfafdfas");
        };
        return (false);

        break;

      case 1:
        if (index == 0)
        {
          stepper1_3.move(-1, 0);
        }
        else
        {
          stepper1_3.move(0, -1);
        }

        posit[index]--;
        pos[index]--;
        reset_pos();
        if (pos[index] <= -800)
        {
          pos[index] = 0;
          return (true);
          Serial.println("0102929929");
        };
        return (false);

        break;
      case 2:
        if (index == 0)
        {
          stepper1_3.move(1, 0);
        }
        else
        {
          stepper1_3.move(0, 1);
        }

        posit[index]++;
        pos[index]++;
        reset_pos();
        if (pos[index] >= 1600)
        {
          pos[index] = 0;
          return (true);
        };
        return (false);
        break;
      }
    }
    else if (index == 1 || index == 3)
    {

      switch (rotate)
      {
      case 0:

        if (index == 1)
        {
          stepper2_4.move(1, 0);
        }
        else
        {
          stepper2_4.move(0, 1);
        }

        posit[index]++;
        pos[index]++;
        reset_pos();
        if (pos[index] >= 800)
        {
          pos[index] = 0;
          return (true);
          Serial.println("dsfafdfas");
        };
        return (false);

        break;

      case 1:
        if (index == 1)
        {
          stepper2_4.move(-1, 0);
        }
        else
        {
          stepper2_4.move(0, -1);
        }

        posit[index]--;
        pos[index]--;
        reset_pos();
        if (pos[index] <= -800)
        {
          pos[index] = 0;
          return (true);
        };
        return (false);

        break;
      case 2:

        if (index == 1)
        {
          stepper2_4.move(1, 0);
        }
        else
        {
          stepper2_4.move(0, 1);
        }

        posit[index]++;
        pos[index]++;
        reset_pos();
        if (pos[index] >= 1600)
        {
          pos[index] = 0;
          return (true);
        };
        return (false);

        break;
      }
      return (false);
    }
  }

  bool Rot(int index, int angle)
  {

    if (index == 0 || index == 2)
    {
      int Way;
      if ((angle - posit[index]) > (posit[index] - angle))
      {
        Way = 1;
      }
      else
      {
        Way = -1;
      }
      if (index == 0)
      {
        stepper1_3.move(Way, 0);
      }
      else
      {
        stepper1_3.move(0, Way);
      }

      posit[index] = posit[index] + Way;

      if (posit[index] == angle)
      {
        reset_pos();
        return (true);
      };
      reset_pos();
      return (false);
    }
    else if (index == 1 || index == 3)
    {
      int Way = 0;
      if ((angle - posit[index]) > (posit[index] - angle))
      {
        Way = 1;
      }
      else
      {
        Way = -1;
      }
      if (index == 1)
      {
        stepper2_4.move(Way, 0);
      }
      else
      {
        stepper2_4.move(0, Way);
      }

      posit[index] = posit[index] + Way;
      if (posit[index] == angle)
      {
        reset_pos();
        return (true);
      };
      reset_pos();
      return (false);
    }
  }
};

Steppers steppers;

void loop()
{
  if (Serial.available() > 0)
  {
    Sinput = Serial.readStringUntil('/n');
    input = Sinput.charAt(0);
  }

  if (input == 'C' || input == 'c')
  {
    calbration(encoder_value);
    input = NULL;
  }
  else if (input == 'H' || input == 'h')
  {
    boolean homing[4];
    for (int i = 0; i < 4; i++)
    {
      homing[i] = center(i);
    }

    int x = 0;
    for (int i = 0; i < 4; i++)
    {
      if (homing[i] = true)
      {
        x++;
      }
    }
    if (x == 4)
    {
      for (int i = 0; i < 4; i++)
      {
        servo[i].write(10);
      }
      delay(7000);
      for (int i = 0; i < 4; i++)
      {
        servo[i].write(88);
      }
      input = ' ';
    }
  }
  else if (input == 'G')
  {

    String Rot_Notation = "";
    Rot_Notation = (Sinput.substring(2));
    int NumberOfNotations = Find_Num_Items(Rot_Notation, ' ');
    String Notation[NumberOfNotations];
    for (int i = 0; i < NumberOfNotations; i++)
    {
      Notation[i] = (getValue(Rot_Notation, ' ', i));
      char Face = Notation[i].charAt(0);
      int Way = 0;
      if (Notation[i].charAt(1) == '\u0027')
      {
        Way = 0;
      }
      else if (Notation[i].charAt(1) == '2')
      {
        Way = 2;
      }
      else
      {
        Way = 1;
      }
      rotation(Face, Way);
      delay(500);
    }
    input = ' ';
    delay(200);
    Serial.write("Fin");
  }
  else if (input == 'T')
  {
    char Face = ' ';
    Face = (Sinput.charAt(2));
    Turn_FaceUp(Face);
    input = ' ';
    Serial.write("Fin");
  }
  else if (input == 'D')
  {
    char Clip = ' ';
    Clip = (Sinput.charAt(2));
    Clip_Open(Clip);
    delay(300 );
    Serial.write("Fin");
    input = ' ';
  }
  else if (input == 'E')
  {
    char Clip = ' ';
    Clip = (Sinput.charAt(2));
    Clip_Close(Clip);
    delay(100);
    Serial.write("Fin");
    input = ' ';
  }
  else if (input == 'R')
  {
    resetIndex();
    input = ' ';
  }
  else if (input == 'F')
  {
    if (Sinput.length() == 4)
    {
      ROT_XYZ(String(Sinput.charAt(2)));
    }
    else
    {
      ROT_XYZ(String(Sinput.charAt(2)) + "'");
    }
    delay(350);
    Serial.write("fin");
    input = ' ';
  }
  if (DEBUG == true)
  {
    for (int i = 0; i < 4; i++)
    {
      encoder_value[i] = analogRead(encoderPin[i]);
      Serial.print(encoder_value[i]);
      Serial.print(",");
    }
    Serial.println("");

    Serial.println("");
  }
}

void Clip_Open(char X_OR_Y)
{
  if (X_OR_Y == 'X')
  {
    servoMove(2, false);
    servoMove(0, false);
  }
  else if (X_OR_Y == 'Y')
  {
    servoMove(1, false);
    servoMove(3, false);
  }
}
void Clip_Close(char X_OR_Y)
{
  if (X_OR_Y == 'X')
  {
    servoMove(2, true);
    servoMove(0, true);
  }
  else if (X_OR_Y == 'Y')
  {
    servoMove(1, true);
    servoMove(3, true);
  }
}
void rotation(char face, int ways)
{
  for (int i = 0; i < 6; i++)
  {
    if (index[i] == face)
    {
      if (i == 4 || i == 5)
      {
        if (i == 4)
        {
          for (int x = 0; x < 2; x++)
          {
            if (steppers.posit[NEIGHBOR[0][x]] == 0 || steppers.posit[NEIGHBOR[0][x]] == 1600)
            {
            }
            else
            {
              returnCTR(NEIGHBOR[0][x]);
            }
          }

          for (int x = 0; x < 2; x++)
          {
            if (steppers.posit[NEIGHBOR[1][x]] == 800 || steppers.posit[NEIGHBOR[1][x]] == 2400)
            {
            }
            else
            {
              To_angle(NEIGHBOR[1][x], 800);
            }
          }

          delay(300);
          servoMove(1, false);
          servoMove(3, false);
          delay(200);
          boolean finish = false;
          while (finish == false)
          {
            boolean fin_1 = false;
            boolean fin_2 = false;
            fin_1 = (steppers.Move(0, 0));
            fin_2 = (steppers.Move(2, 1));
            finish = fin_1 && fin_2;
          } 
          servoMove(1, true);
          servoMove(3, true);
          delay(300);
          boolean fin_1 = false;
          while (fin_1 == false)
          {
            fin_1 = (steppers.Move(1, ways));
          }
          char index_cp[6];
          for (int i = 0; i < 6; i++)
          {
            index_cp[i] = index[i];
          }
          index[1] = index_cp[4];
          index[4] = index_cp[3];
          index[3] = index_cp[5];
          index[5] = index_cp[1];
        }
        else
        {
          for (int x = 0; x < 2; x++)
          {
            if (steppers.posit[NEIGHBOR[0][x]] == 0 || steppers.posit[NEIGHBOR[0][x]] == 1600)
            {
            }
            else
            {
              returnCTR(NEIGHBOR[0][x]);
            }
          }
          for (int x = 0; x < 2; x++)
          {
            if (steppers.posit[NEIGHBOR[1][x]] == 800 || steppers.posit[NEIGHBOR[1][x]] == 2400)
            {
            }
            else
            {
              To_angle(NEIGHBOR[1][x], 800);
            }
          }

          delay(300);
          servoMove(1, false);
          servoMove(3, false);
          delay(300);
          boolean finish = false;
          while (finish == false)
          {
            boolean fin_1 = false;
            boolean fin_2 = false;
            fin_1 = (steppers.Move(0, 1));
            fin_2 = (steppers.Move(2, 0));
            finish = fin_1 && fin_2;
          }

          servoMove(1, true);
          servoMove(3, true);
          delay(300);
          boolean fin_1 = false;
          while (fin_1 == false)
          {
            fin_1 = (steppers.Move(1, ways));
          }
          char index_cp[6];
          for (int i = 0; i < 6; i++)
          {
            index_cp[i] = index[i];
          }
          index[1] = index_cp[5];
          index[3] = index_cp[4];
          index[4] = index_cp[1];
          index[5] = index_cp[3];
        }
      }
      else
      {
        for (int x = 0; x < 2; x++)
        {
          if (steppers.posit[NEIGHBOR[i][x]] == 0 || steppers.posit[NEIGHBOR[i][x]] == 1600)
          {
          }
          else
          {
            returnCTR(NEIGHBOR[i][x]);
          }
        }
        boolean fin = false;
        delay(300);
        while (fin == false)
        {
          fin = steppers.Move(i, ways);
        }
      }
    }
  }
  delay(300);
}

void calbration(int env[4])
{
  for (int i = 0; i < 4; i++)
  {
    setting.en_cen_value[i] = env[i];
  }
}

void returnCTR(int index)
{
  servoMove(index, false);
  delay(100);
  boolean fin_1 = false;
  if (abs(1600 - steppers.posit[index]) < steppers.posit[index])
  {
    while (fin_1 == false)
    {
      fin_1 = (steppers.Rot(index, 1600));
    }
  }
  else
  {
    while (fin_1 == false)
    {
      fin_1 = (steppers.Rot(index, 0));
    }
  }
  servoMove(index, true);
  delay(300);
}

void servoMove(int index, bool EN)
{
  if (EN == true)
  {
    servo[index].write(87);
  }
  else if (EN == false)
  {
    servo[index].write(20);
  }
}

void To_angle(int index, int angle)
{
  servoMove(index, false);
  delay(100);
  boolean fin_1 = false;
  if (angle == 800)
  {
    if (abs(2400 - steppers.posit[index]) < abs(800 - steppers.posit[index]))
    {

      while (fin_1 == false)
      {
        fin_1 = (steppers.Rot(index, 2400));
      }
    }
    else
    {
      while (fin_1 == false)
      {
        fin_1 = (steppers.Rot(index, 800));
      }
    }
  }
  else
  {
    while (fin_1 == false)
    {
      fin_1 = (steppers.Rot(index, angle));
    }
  }
  servoMove(index, true);
  delay(300);
}

void Turn_FaceUp(char Face)
{
  int OPPOSTIE[4][2] = {{0, 2}, {1, 3}, {2, 0}, {3, 1}};
  for (int i = 0; i < 4; i++)
  {
    if (index[i] == Face)
    {
      for (int x = 0; x < 2; x++)
      {
        if (steppers.posit[OPPOSTIE[i][x]] == 0 || steppers.posit[OPPOSTIE[i][x]] == 1600)
        {
        }
        else
        {
          returnCTR(OPPOSTIE[i][x]);
        }
      }
      for (int x = 0; x < 2; x++)
      {
        if (steppers.posit[NEIGHBOR[i][x]] == 800 || steppers.posit[NEIGHBOR[i][x]] == 2400)
        {
        }
        else
        {
          To_angle(NEIGHBOR[i][x], 800);
        }
      }

      delay(300);
      servoMove(OPPOSTIE[i][0], false);
      servoMove(OPPOSTIE[i][1], false);
      delay(100);
      boolean finish = false;
      int LeftM_rotation = 0;
      int RightM_rotation = 0;
      while (finish == false)
      {

        for (int x = 0; x < 2; x++)
        {
          if (NEIGHBOR[NEIGHBOR[i][0]][x] == i)
          {

            LeftM_rotation = (x == 0) ? 1 : 0;
          }
          if (NEIGHBOR[NEIGHBOR[i][1]][x] == i)
          {
            RightM_rotation = (x == 0) ? 1 : 0;
          }
        }
        boolean fin_1 = false;
        boolean fin_2 = false;
        fin_1 = (steppers.Move(NEIGHBOR[i][0], LeftM_rotation));
        fin_2 = (steppers.Move(NEIGHBOR[i][1], RightM_rotation));
        finish = fin_1 && fin_2;
      }
      servoMove(OPPOSTIE[i][0], true);
      servoMove(OPPOSTIE[i][1], true);
      char index_cp[6];
      for (int i = 0; i < 6; i++)
      {
        index_cp[i] = index[i];
      }
      switch (i)
      {
      case 0:
        index[4] = index_cp[0];
        index[0] = index_cp[5];
        index[5] = index_cp[2];
        index[2] = index_cp[4];
        break;
      case 1:
        index[4] = index_cp[1];
        index[1] = index_cp[5];
        index[5] = index_cp[3];
        index[3] = index_cp[4];
        break;
      case 2:
        index[4] = index_cp[2];
        index[2] = index_cp[5];
        index[5] = index_cp[0];
        index[0] = index_cp[4];
        break;
      case 3:
        index[4] = index_cp[3];
        index[3] = index_cp[5];
        index[5] = index_cp[1];
        index[1] = index_cp[4];
        break;
      }
    }
  }
}
int Find_Num_Items(String data, char separator)
{
  int found = 0;
  int maxIndex = data.length() - 1;

  for (int i = 0; i <= maxIndex && found <= index; i++)
  {
    if (data.charAt(i) == separator || i == maxIndex)
    {
      found++;
    }
  }
  return found;
}

String getValue(String data, char separator, int index)
{
  int found = 0;
  int strIndex[] = {0, -1};
  int maxIndex = data.length() - 1;

  for (int i = 0; i <= maxIndex && found <= index; i++)
  {
    if (data.charAt(i) == separator || i == maxIndex)
    {
      found++;
      strIndex[0] = strIndex[1] + 1;
      strIndex[1] = (i == maxIndex) ? i + 1 : i;
    }
  }

  return found > index ? data.substring(strIndex[0], strIndex[1]) : "";
}

boolean center(int module)
{
  int encoder_angle = 0;
  if (module == 0)
  {
    boolean Homed = false;
    for (int i = 0; i < 4; i++)
    {
      servo[i].write(88);
    }
    servo[module].write(40);
    for (int i = 0; i < 3200; i += 1)
    {
      if (Homed == false)
      {
        stepper1_3.move(i, 0);
      }
      encoder_angle = analogRead(encoderPin[module]);
      if (abs(setting.en_cen_value[module] - encoder_angle) < 10)
      {
        Homed = true;
        return (true);
      }
      else
      {
      }
    }
  }
  if (module == 1)
  {
    boolean Homed = false;
    for (int i = 0; i < 4; i++)
    {
      servo[i].write(88);
    }
    servo[module].write(20);
    for (int i = 0; i < 3200; i += 1)
    {
      if (Homed == false)
      {
        stepper2_4.move(i, 0);
      }
      encoder_angle = analogRead(encoderPin[module]);
      if (abs(setting.en_cen_value[module] - encoder_angle) < 10)
      {
        Homed = true;
        return (true);
      }
      else
      {
      }
    }
  }
  if (module == 2)
  {
    boolean Homed = false;
    for (int i = 0; i < 4; i++)
    {
      servo[i].write(88);
    }
    servo[module].write(20);
    for (int i = 0; i < 3200; i++)
    {
      if (Homed == false)
      {
        stepper1_3.move(0, (i));
      }
      encoder_angle = analogRead(encoderPin[module]);
      (300);
      if (abs(setting.en_cen_value[module] - encoder_angle) < 10)
      {
        Homed = true;
        return (true);
      }
      else
      {
      }
    }
  }
  if (module == 3)
  {
    boolean Homed = false;
    for (int i = 0; i < 4; i++)
    {
      servo[i].write(88);
    }
    servo[module].write(20);
    for (int i = 0; i < 3200; i++)
    {
      if (Homed == false)
      {
        stepper2_4.move(0, (i));
      }
      encoder_angle = analogRead(encoderPin[module]);
      if (abs(setting.en_cen_value[module] - encoder_angle) < 10)
      {
        Homed = true;
        return (true);
      }
      else
      {
      }
    }
  }
}


void resetIndex()
{
  char RefactorIndex[6] = {'L', 'B', 'R', 'F', 'U', 'D'};
  for (int x = 0; x < 6; x++)
  {
    index[x] = RefactorIndex[x];
  } 
}

void ROT_XYZ(String ways)
{
  resetIndex();
  if (ways.length() == 1)
  {
    switch (ways.charAt(0))
    {
    case 'X':
      Turn_FaceUp('L');
      break;
    case 'Y':
      Turn_FaceUp('F');
      break;
    case 'Z':
      Turn_FaceUp('F');
      Turn_FaceUp('L');
      Turn_FaceUp('U');
      break;
    }
  }
  else
  {
    switch (ways.charAt(0))
    {
    case 'X':
      Turn_FaceUp('R');
      break;
    case 'Y':
      Turn_FaceUp('B');
      break;
    case 'Z':
      Turn_FaceUp('F');
      Turn_FaceUp('R');
      Turn_FaceUp('U');
      break;
    }
  }
  resetIndex();
}

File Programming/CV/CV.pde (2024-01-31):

import processing.video.*; //<>// //<>// //<>// //<>// //<>// //<>// //<>// //<>// //<>// //<>// //<>// //<>//
import processing.serial.*;
import http.requests.*;
import controlP5.*;
import gab.opencv.*;
import processing.sound.*;


// 130 171 199 102
OpenCV opencv;

ControlP5 GUI; 

Serial Solver;   

Capture cam; 

boolean StartSolve = false;
int[]FaceColor = new int[9];//FaceColor RAM
char Cube_Color[][][] = new char[6][3][3];//whole Cube color
color[]face_color = {#9B2D2D, #A0F0A0, #00A0F0, #F0F050, #F0A000, #ffffff}; 
// red green blue yellow orange white(this value compare with camera)
color[]src = {#BC1B12,#6CB176,#00668F, #EED275, #D76007, #DEDFC3}; 
color[]Corsrc = {#BC1B12,#6CB176,#00668F, #EED275, #D76007, #DEDFC3}; 

boolean debug = true; //Use to adjust the Corsrc and src
boolean PDraw_rect = false;

//Calbration part(value)
int mstartx, mstarty; 
int[]Detectx = new int[9];
int[]Detecty = new int[9];
int[]Detectcornx = new int[9];
int[]Detectcorny = new int[9];
int cal_counter = 0;
boolean cal = false;
boolean Auto_cal = false;
boolean Tragged = false;
boolean Released = false;
boolean Pressed = false;
//Calbration part(value) END

SoundFile Finish_Sound;

color[] OriginalColorptNineRes = new color[9];//average color value of a area
color[] OriginalColorpt = new color[9];

//Cube drawing
int box_size = 80;
rubikCube rubik = new rubikCube();
//Cube drawing END

boolean Solving = false;
boolean Scanning = false;  

color PIXELS[][] = new color[640][480]; // From pixel[] to PIXELS[][]


void setup() {
  //Serial port
  // printArray(Serial.list());
  Solver = new Serial(this, Serial.list()[4], 115200);
  //Serial portEND

  //Camera
  String[] cameras = Capture.list();
  printArray(cameras);
  delay(1000);
  cam = new Capture(this, cameras[2]);
  cam.resize(640, 480);
  cam.start();
  //Camera END

  //calbration part
  String[] x = loadStrings("calbrationx.txt");
  String[] y = loadStrings("calbrationy.txt");
  String[] Conx = loadStrings("calbrationConx.txt");
  String[] Cony = loadStrings("calbrationCony.txt");
  Detectx = int(x);
  Detecty = int(y);
  Detectcorny = int(Cony);
  Detectcornx = int(Conx);



  //create a new button with name 'buttonA'
  textSize(90); 
  //PFont  font = new PFont();
  //font = createFont("andalemo.ttf", 60);
  textSize(32);
  //PFont text = new Font("andalemo.ttf", 32);
  //textFont(text);
  PFont font1 = createFont("beef'd.ttf", 14);
  PFont font2 = createFont("beef'd.ttf", 11);

  //GUI
  GUI = new ControlP5(this);
  GUI.addButton("Solve")
    .setPosition(700, 600)
    .setSize(180, 50)
    .setFont(font1)
    .activateBy(ControlP5.RELEASE)
    ;
  //Celebrate Song
  Finish_Sound = new SoundFile(this, "never-gonna-give-you-up-video.mp3");


  size(980, 740);
  colorMode(RGB, 255);
}


PImage CAM;
int ha = 0;
void draw() {

  //setup(START)
  imageMode(CENTER);
  background(255);

  //setup(END)



  //calibration
  if (cal ==  true) {
    background(255);
    cam.read();
    image(cam, width / 2, height / 2, 640, 480);
    if (PDraw_rect != Draw_rect) {
      if (Draw_rect == true) {
        PDraw_rect = Draw_rect;
      } 
      mstartx = mouseX;
      mstarty = mouseY;
    }
    calbration();
  } else if (Scanning == true) {
    println("Scanning...");
    //for (int i = 0; i< 3; i++) {
    if (Scan() == true) { // When not error occurs
      Scanning = false;
      Solving = true;
    } else {
      Scanning = false;
      Solver.write("T B");
      Solver.write('\n');
      Solver.clear();
      delay(100);
      println("Error Occurs, Press S to try again");
    }
  } else if (Solving == true) {
    println("Solving...");
    rubikCube ProVer = new rubikCube();
    rubikCube PyVer = new rubikCube();

    ProVer = Rotate_Cube_To_Pro();
    PyVer = Rotate_Cube_To_Py();
    Put(ProVer.To_String(), PyVer.To_String());
    //waiting for solve
    int ID = GetSolvedIndex();
    while (ID == -1) {
      ID = GetSolvedIndex();
      delay(300);
    }
    GetRequest get = new GetRequest("http://localhost:3000/data");
    get.send();
    StartSolve = false;
    // while (StartSolve == false);
    if (ID == 1) {
      String[] XYZROT =  split(ProstateComment, ' ');
      for (int i = 0; i < XYZROT.length; i++) {
        Solver.write("F " + XYZROT[i]);
        println("F " + XYZROT[i]);
        Solver.clear();   
        Solver.write('\n');
        while (Solver.readString() ==  null) {
          delay(300);
        }
        Solver.clear();        
        delay(300);
      }
      rubik = ProVer;
    } else {
      String[] XYZROT =  split(PystateComment, ' ');

      for (int i = 0; i < XYZROT.length; i++) {
        Solver.write("F " + XYZROT[i]);
        println("F " + XYZROT[i]);
        Solver.write('\n');
        while (Solver.readString() ==  null) {
          delay(200);
        }
        Solver.clear();        
        delay(200);
      }
      rubik = PyVer;
    }
    Solver.clear();
    JSONObject response = parseJSONObject(get.getContent());
    String Solution = (response.getString("Cube_Solution"));
    delay(200);

    int start = 0;
    int end = 10;
    for (int  i = 0; i < ceil(float(Solution.length()) / 100); i++) {
      if (i == (ceil(float(Solution.length()) / 100) - 1)) {
        Solver.write("G " + (Solution.substring(start, Solution.length())));
        Solver.write('\n');
      } else {
        Solver.write("G " + (Solution.substring(start, end)));
        Solver.write('\n');
      }
      start += 10;
      end += 10;
      while (Solver.readString() ==  null) {
        delay(200);
      }
      Solver.clear();
    }



    Solving = false;
    println("----------------Solved-------------------");
    println("----------------Solved-------------------");
    println("----------------Solved-------------------");
    println("----------------Solved-------------------");
    rubik = new rubikCube();
    Finish_Sound.play();
  } else if (Auto_cal == true) {
    cam.read();
    auto_Calbration(cam);
  } else {
    FaceDetect();
    rubik.drawCube();

    if (debug == true) {
      for (int i = 0; i < 9; i++) {
        print(hex(FaceAverage(Detectx[i], Detecty[i], Detectcornx[i], Detectcorny[i]), 6));
        print(",");
      }
      println("");
    } else {
      for (int i = 0; i < 9; i++) {
        textSize(20);
        textAlign(CENTER);
      }
    }
  }
  Released = false;
  Tragged = false;
}


void mouseDragged() {
  Tragged = true;
}

void mouseReleased() {
  Released = true;
  StartSolve = true;
}


float deltaD(color compared, color source) {
  float RC = 2;
  float GC = 4;
  float BC = 3;

  float comR = red(compared);
  float comG = green(compared);
  float comB = blue(compared);
  float sourceR = red(source);
  float sourceG = green(source);
  float sourceB = blue(source);

  float r = (comR + sourceR) / 2;
  float diffR = sq(comR - sourceR);
  float diffG = sq(comG - sourceG);
  float diffB = sq(comB - sourceB);

  return sqrt(2 * diffR + 4 * diffG + 3 * diffB);
}
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

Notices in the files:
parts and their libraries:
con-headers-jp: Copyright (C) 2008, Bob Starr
